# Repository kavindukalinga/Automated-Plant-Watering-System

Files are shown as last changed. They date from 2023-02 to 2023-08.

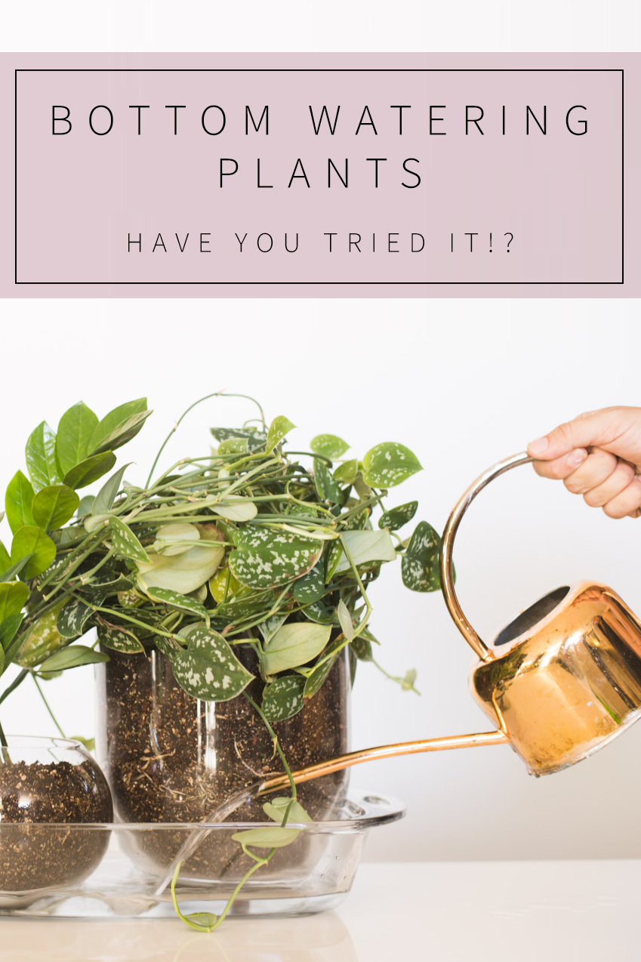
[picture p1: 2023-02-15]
Bottom-Watering-Plants.jpg

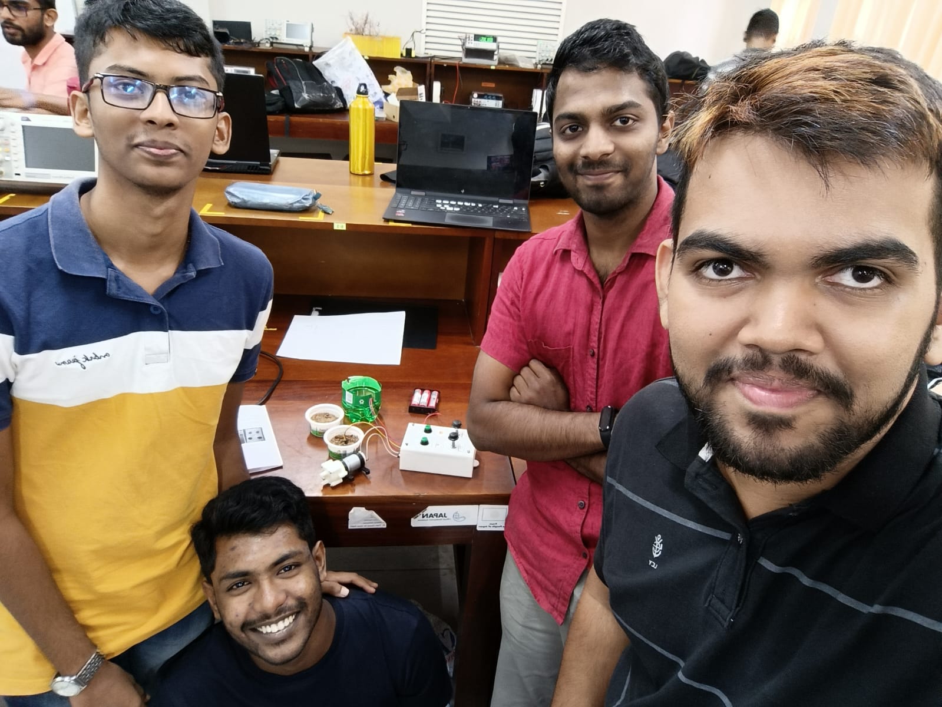
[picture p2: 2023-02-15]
Team - En04.jpg

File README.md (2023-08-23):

# Automated Plant Watering System 
 This is the project we chose for the Engineering design project module in semester 2. (In20-S2-EN1190 - Engineering Design Project)
 
# our project 

## Abstract:
The Automated Plant Watering System is designed to be used in home gardening to water plants when the moisture level in the soil drops below a certain level. Our main objective for this project is to provide a perfect solution for the problem that we identified, and the product that we develop should be cost-effective, easily repairable, and durable. In order to realize the design, we used software such as CircuitLab, Altium, and SolidWorks. The circuit simulation is checked using the CircuitLab simulator. The PCB design is done using the Altium software, and the enclosure is designed using SolidWorks software.

## Introduction:
The Automated Plant Watering System is an innovative solution designed to provide efficient and reliable watering for plants. The system is a response to the economic crisis in Sri Lanka and the need to encourage people to cultivate their own food. Many people are unable to tend to their plants due to busy schedules, leading to plant death. The Automated Plant Watering System is an easy-to-use system that automates the process of watering plants, ensuring their growth and health.

## Functionality:
The Automated Plant Watering System is a complete analog electronic system that detects soil moisture and the amount of water in the tank. It is designed to operate based on soil moisture readings and water availability in the tank. The system has a sensor that detects the moisture in the soil and signals the motor to distribute water to the soil if it is dry. The motor is connected using a relay module, which controls the water flow to the plants. The system also has a water level sensor that detects the amount of water in the tank. If the water level in the tank is low, an alarm is triggered to alert the user. The alarm is manually turned off by the user when the water is refilled. The system also has a timer that the user can adjust to control the water flow to the plants.

## User Interface:
The Automated Plant Watering System has an easy-to-use user interface that consists of two buttons and two knobs. The first button turns on the system, and the second button turns on/off the alarm. The first knob is used to control the timer, and the second knob is used to adjust the soil sensitivity. The soil sensitivity knob adjusts the dryness of the soil that should be present before the system starts watering the plants. The system is user-friendly and requires minimal effort from the user.

## Conclusion:
In conclusion, the Automated Plant Watering System is an efficient and innovative solution to the economic crisis in Sri Lanka. It is an easy-to-use system that automates the process of watering plants and ensures their growth and health. The system is designed to operate based on soil moisture readings and water availability in the tank. The user interface is simple and requires minimal effort from the user. The Automated Plant Watering System is a cost-effective solution that promotes sustainable living and encourages people to cultivate their own food.  

### Visit My Blog [Here](https://kalingachandrasiri.blogspot.com/2023/02/automated-plant-watering-system.html)

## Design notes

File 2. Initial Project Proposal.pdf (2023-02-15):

# Automated Plant Watering System

## PRODUCT PROPOSAL

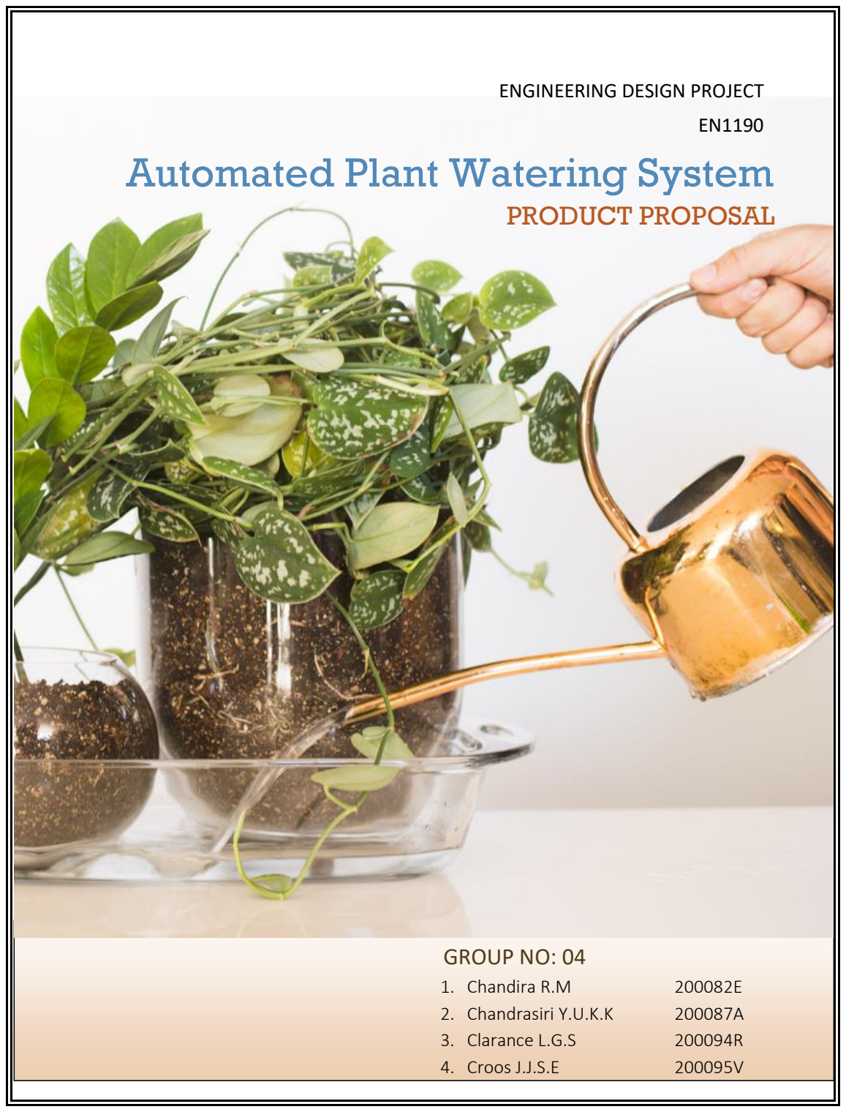
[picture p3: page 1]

ENGINEERING DESIGN PROJECT EN1190

## GROUP NO: 04

1. Chandira R.M | 200082E
2. Chandrasiri Y.U.K.K | 200087A
3. Clarance L.G.S | 200094R
4. Croos J.J.S.E | 200095V

## PROBLEM

Due to the prevailing economic instability in our country, there is an urgent need to increase the national production rate. To suppress the food crisis government has advised public to engage in home gardening. But it appears to many as a impossible task to manage this among their busy schedules.

## SOLUTION

Proposed solutions,

1. Greenhouse control system
2. User notifier on taking care of plants
3. Automated plant watering system

We finally agreed on developing an automated plant watering system.

## GOAL

Our main goal is to encourage people for more home gardening at least to meet their daily needs in the time of this crisis and beyond. We wish to develop this product affordable as much as possible while people in our country going through an economic crisis. This product will be user friendly, easy to repair and easy to reproduce with less resources.

## TARGET USERS

Government and Private sector workers, especially low-income people

## DESIGN SPECIFICATION

Our sensors are measuring the moisture level of soil and when the soil get dried than the threshold level, it triggers the irrigation system to water the plant.
And this automated system notifies the user to refill the water reservoir when the water level is low. And our whole electronic and electrical components of our system is protected by enclosure which is watertight and have resistance to all damaging factors of both indoor and outdoor environment. This system is friendly, in case of any repairing the user can easily access it.

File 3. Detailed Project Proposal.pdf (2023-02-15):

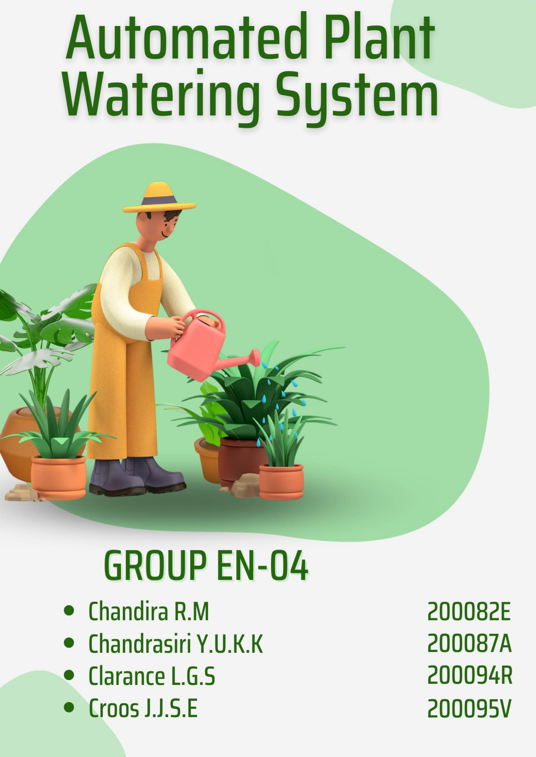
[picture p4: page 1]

# Content

## 1.Introduction

## 2.Proposed Solutions

## 3.Idea Validation

## 4. Survey Results

## 5.Technical Specifications

## 6.Technical Feasibility

## 7.Product Architecture

## 8. Enclosure Design

## 9.Marketing and Sales and Beyond

## 10.Project Budget

## Introduction

Due to the prevailing economic crisis in our country, we are facing unprecedented food shortages, so there is an urgent need to increase the national production rate to overcome food scarcity and malnutrition among children. To suppress this food crisis, the government has advised the public to engage in home gardening. “Amid the fuel crisis and looming food crisis, the government has decided to declare Friday as a holiday for State employees except for those who are engaged in providing essential services and to allow them to engage in agricultural activities in their home gardens." - [published on DailyMirror 15th June 2022]. By doing home gardening, people will get their daily essential nutrition at a minimum cost. But it appears to many (government and private sector workers) as an unthinkable task to manage this among their busy schedules because home gardening is something that needs continuous monitoring and extensive care.

So, as undergraduates of the Electronic and Telecommunication Department, University of Moratuwa, we are planning to design an electronic device which can be used as a solution to this problem, and we are very much concerned about the cost because the device that we are constructing should be affordable for everyone, including low-income receivers.

## Proposed Solutions

After brainstorming, we have arrived at some feasible options that can be done within an 8 - 10 weeks period.

### 1. Greenhouse control system:

An automated system targeting greenhouses to monitor and control humidity, temperature, and nutrition levels required for plants. This is done by using real-time sensors and IoT things that communicate wirelessly through Bluetooth or WiFi.

### 2. User notifier on taking care of plants:

An automated system to remind the user to water and add appropriate nutrition to plants. This can be accomplished by developing a device with a system that can send push notifications to the user's mobile.

### 3. Automated Plant Watering System:

Automatic plant watering systems that can water plants when the moisture level in the soil drops below a certain level (which can be adjusted by the user) and notify the user to refill the watering container.

## Idea Validation

When we enquired about the problem, we got some solutions. But every solution will not be executed perfectly. There are many reasons for each solution to be avoided.

When considering the greenhouse as a solution, according to the current price rate (24.06.2022), the cheapest functional greenhouse requires around 35000 LKR to assemble. In the case of repairing, the cost of the repair is also high, like its price. which is a three-quarter of many government staff's salaries. Because of the initial investment, it is not suitable for low-income families.

We need a backyard to set up a greenhouse. But most middle-class families don't have a backyard because most of them are in apartments, and others have limited space.

And there are some products, like

1. Garden cloche, 6 pack plant protect bell cover mini greenhouse (Rs 8,266)
2. Portable garden greenhouse outdoor warm greenhouse (Rs.19,260)

and more. Nothing is easily affordable for low-income families.

The second solution, developing a system to notify the user about watering plants and adding enough nutrition on time, had to be disregarded because of the availability of such apps in the marketplace. There are many apps available, but only a very few can be used without any hassle. Here the problem is, even if we are reminded to water the plant, when we out of home, it is not useful all the time, So we had to avoid these options.
Among all the solutions we had, we came up with designing the “Automated plant watering system” after we researched all our solutions very thoroughly. We considered mainly the cost per product, durability, repairability, and customizability. While we are comparing our product with other solutions and the products currently available in the market, the price of our product is the key factor to attract buyers so we figured out that we would be able to design our product very much affordable when we compared it with the cost of other similar products in the market. And when people buy a product, they should be able to repair it quickly if there are some minor issues. In our case, the product can be easily repaired and has less complexity than other products. For example, if there are issues with greenhouses, it is very hard to get them back to their original condition and it will cost a high amount as well. With this Automated plant watering system, we can water and maintain home gardens in 1m2 area, so it can be manageable in apartments. And it will be easy to reproduce with fewer resources.
Unlike other similar products which are already on the market, components and parts of our product are available in the local market. Therefore, users can replace parts very easily. This product is designed to be splash and dust-proof. The enclosure will protect circuits and electronic components from dry and wet environments.
And our product is easily customizable as well. Users can customize the water level, notifications, and some other stuff as they want, unlike other fixed products and application software.

Even though it is a low-cost product, it can be upgradable according to budget and user expectations. We are planning to add a timer as a refinement to our product, so it will allow our product to work only for a limited time each day, so it can save water and other resources. And we are discussing adding a feature to adjust the volume of water released by the system according to the specific plants. Plants should not be watered too much or too little. In hot weather, it may be tempting to repeatedly water plants, which can adversely affect plant growth. Hence, controlling watering frequency and amount appropriately with a product like ours is a must.
In conclusion, after thorough research using several media, the initial project idea was refined and redefined to better suit the current requirements of the intended users.

## Survey Results

After we built up our idea, we wanted to know about the real situation among our targeted people. So, we conducted a survey through Google Form. The survey is enough to justify our proposed problem and our finalized solution. So we came out of our assumption and strongly moved through it with the evidence of the survey. We finalized our decision with the responses of 170 targeted users.

From the conducted survey, more than three fourth of the population currently engages in home gardening.

Most of the respondents were informed that sometimes they have time to take care of their plants, which is not ideal for cultivation. Many plants, at their young age, are highly sensitive to the rate of watering. Without taking care of such plants daily, they can yield poor crops. Hence, it is clear from our responses that people are not inclined to invest in taking care of their plants consistently, and the need for a product like an automatic plant watering system is very high.

Figure 1: Responses on engaging in home gardening

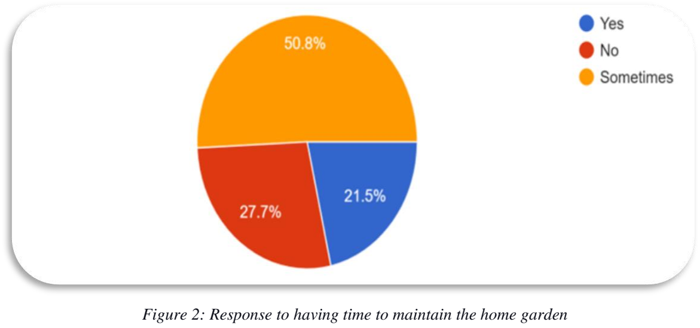
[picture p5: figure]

Even though similar products are widely present in the market, a significant number of responses indicate a preference for a low-cost automatic plant watering system.

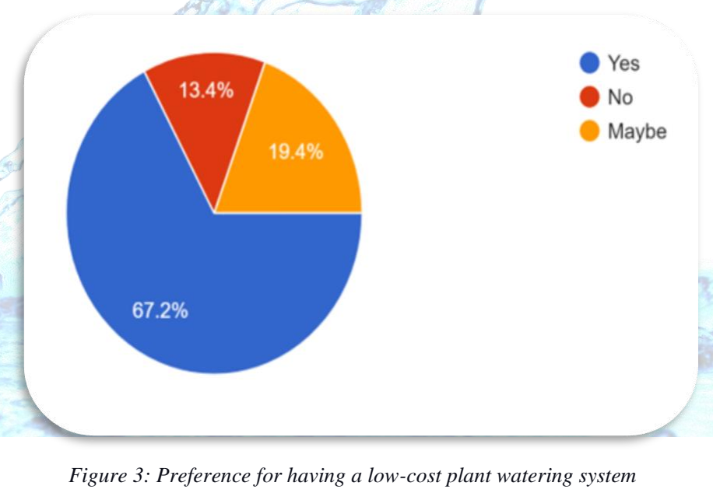
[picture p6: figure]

Our initial plan was to build a system where users needed to check the water level of the container and refill as required to reduce the cost. But the survey showed users prefer to be notified when the water level is empty as it reduces user intervention in plant maintenance.

Figure 2: Response to having time to maintain the home garden

Figure 3: Preference for having a low-cost plant watering system

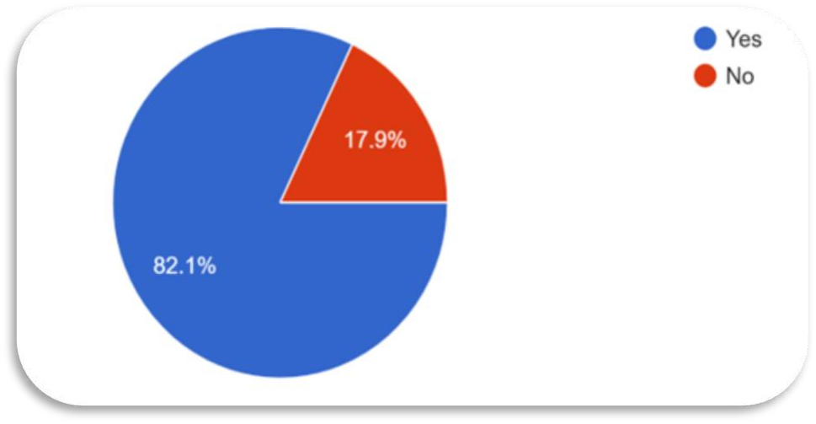
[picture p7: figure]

## Technical Specifications

Performance in quantitative terms.

NE555 timer initial error of timing -3%

Power consumption

LM324 – +/- 60mA, 9V

NE555 – 250mA, 9V

Motor – 12V, 8W

Product dimensions 120mm * 80mm *25mm

Weight - 250g

Lifetime of the product: 6 months for circuit

Warranty terms:

1. The product is only splash resistant to water and does not expose the system to water for extended periods of time.
2. Any physical damage done by the user will not be covered under the warranty.
3. Water pumps that receive no warranty should immerse the pump in a water reservoir while in use.

Figure 4: Preference for the ability of the system to notify when the

## Technical feasibility

Performance requirements

The system is an analogue system; hence it needs no software implementation.

The timer circuit can provide a pulse for up to 11 ms.

The sensitivity of the probes (soil) can be adjusted and probes for water sensitivity is calibrated while preparing the circuit but can be tuned by the user if required.

The motor is capable of pumping water up to 5 m vertically at a flow rate of 600L/H.

The system can provide up to 1.5 liters of water per single operation.

## Product Architecture

### Block diagram

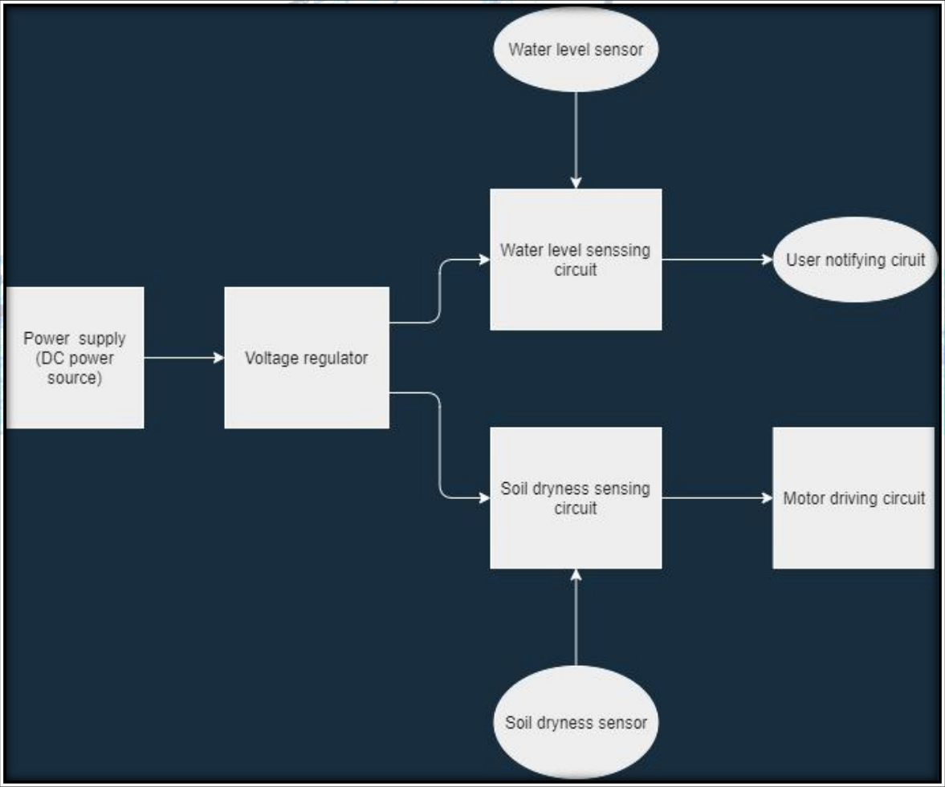
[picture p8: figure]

Figure 5: Block diagram representation

### Circuit Diagram

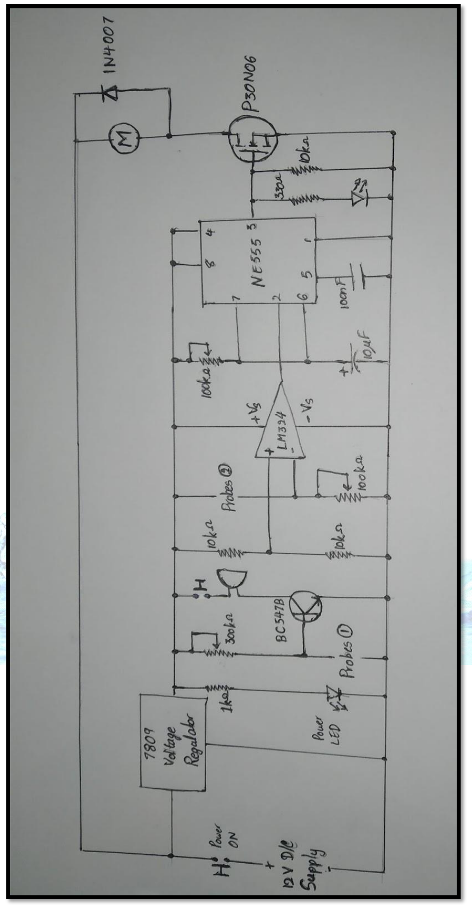
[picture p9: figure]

Figure 6: Circuit

## Enclosure Design

The enclosure contains two knobs (to control soil dry sensitivity and watering duration), two holes for 2 LEDs (indicates Power ON and motor ON), two push switches (Power On/Off and water sound On/Off), a wire connector (6 wires), and a wire connector for power supply. Inside, it contains 4 plugs, which we can use to connect the lid to the cover.
The size of the enclosure only depends on the size of the PCB and other circuit components, so there will not be a massive enclosure. It is a very lightweight one with an easy-to-handle size.
- Color: Mostly Gray and Black
- Material: Plastic

### UI and UX

There is a push switch (Power On/OFF) to Power On the product. When the product is powered on, the LED (Power On) will be on.
There are 2 knobs to control soil dry sensitivity and watering duration. The user needs to adjust the soil dry sensitivity according to the nature of the soil and the watering duration according to the nature of the plant.
The other LED is for indicating that the motor is whether On or Off. The LED is On while the motor is On. Otherwise, it is Off.
The other push switch is for controlling the buzzer. The buzzer is activated when the water level is low. If the user wants to deactivate the buzzer, they can do so using the push button. We label every UI control so that users will not get confused while using it, and it has a very easy-to-use UI.

### Initial Sketches

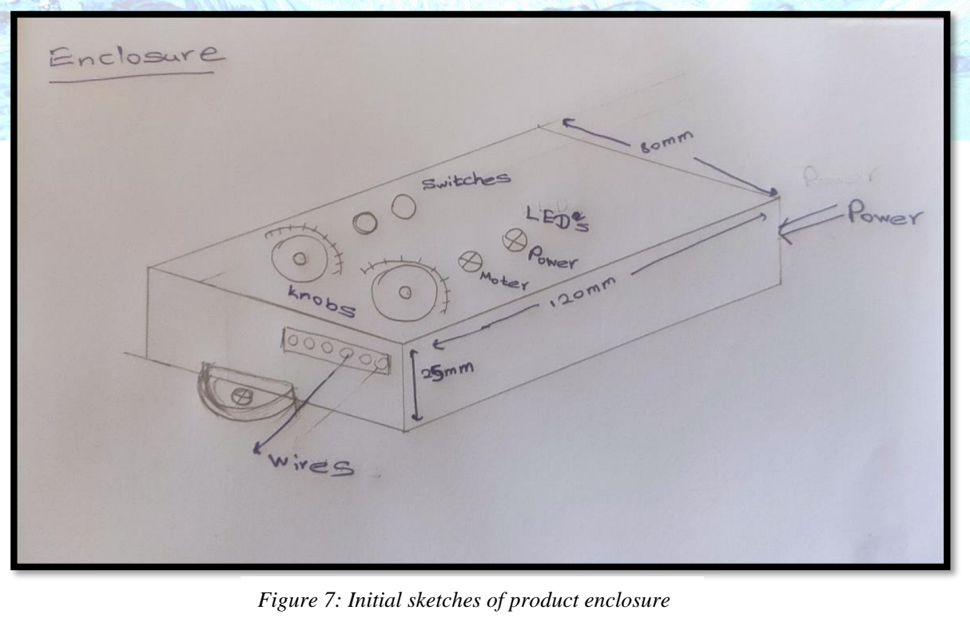
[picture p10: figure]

Figure 7: Initial sketches of product enclosure

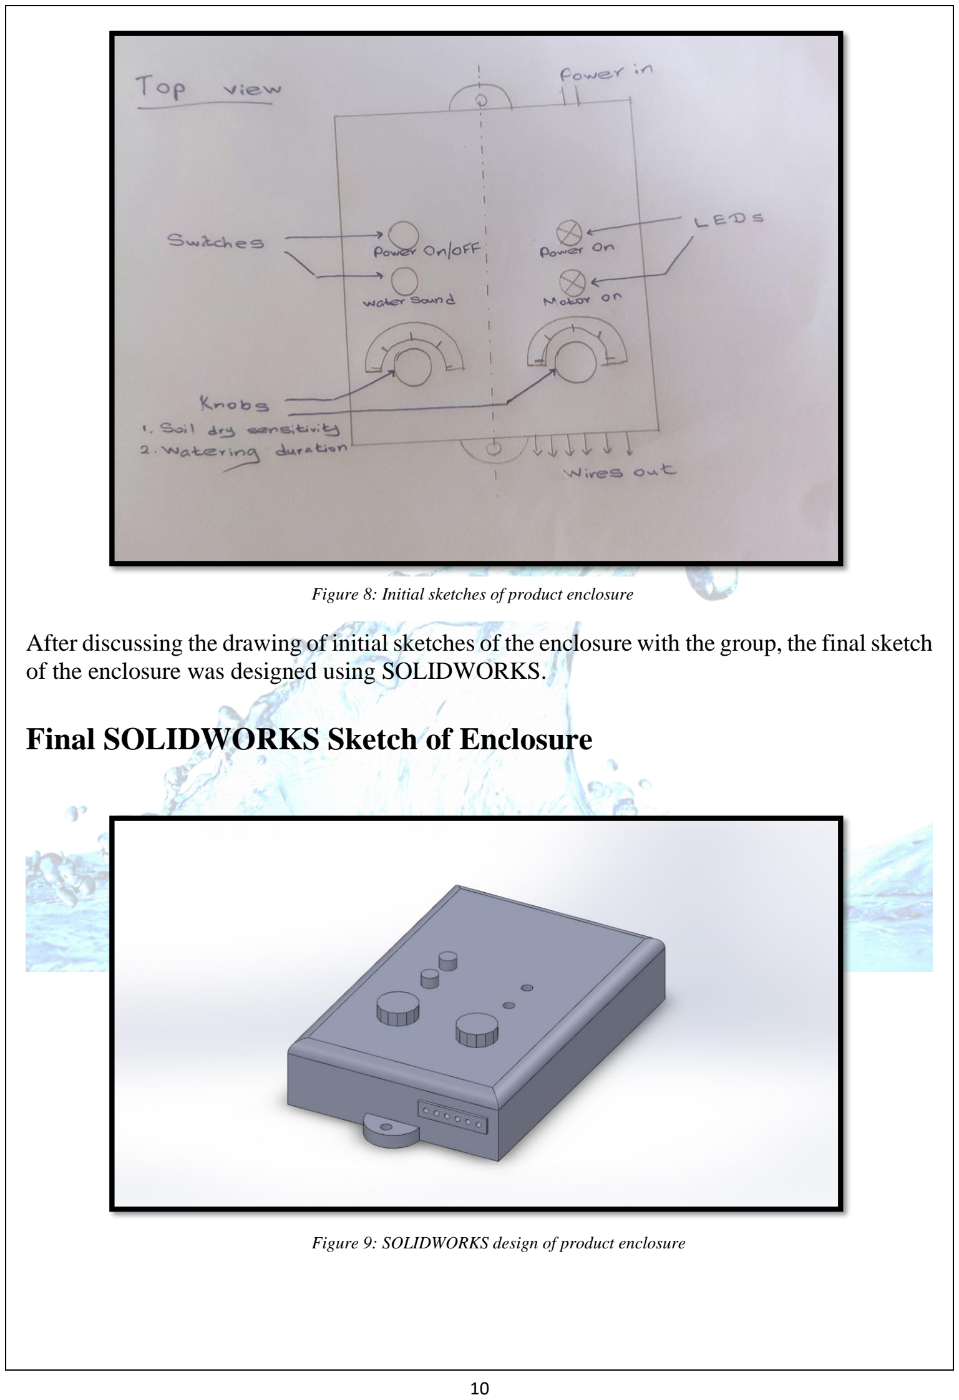
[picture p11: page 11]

After discussing the drawing of initial sketches of the enclosure with the group, the final sketch of the enclosure was designed using SOLIDWORKS.

### Final SOLIDWORKS Sketch of Enclosure

Figure 8: Initial sketches of product enclosure

Figure 9: SOLIDWORKS design of product enclosure

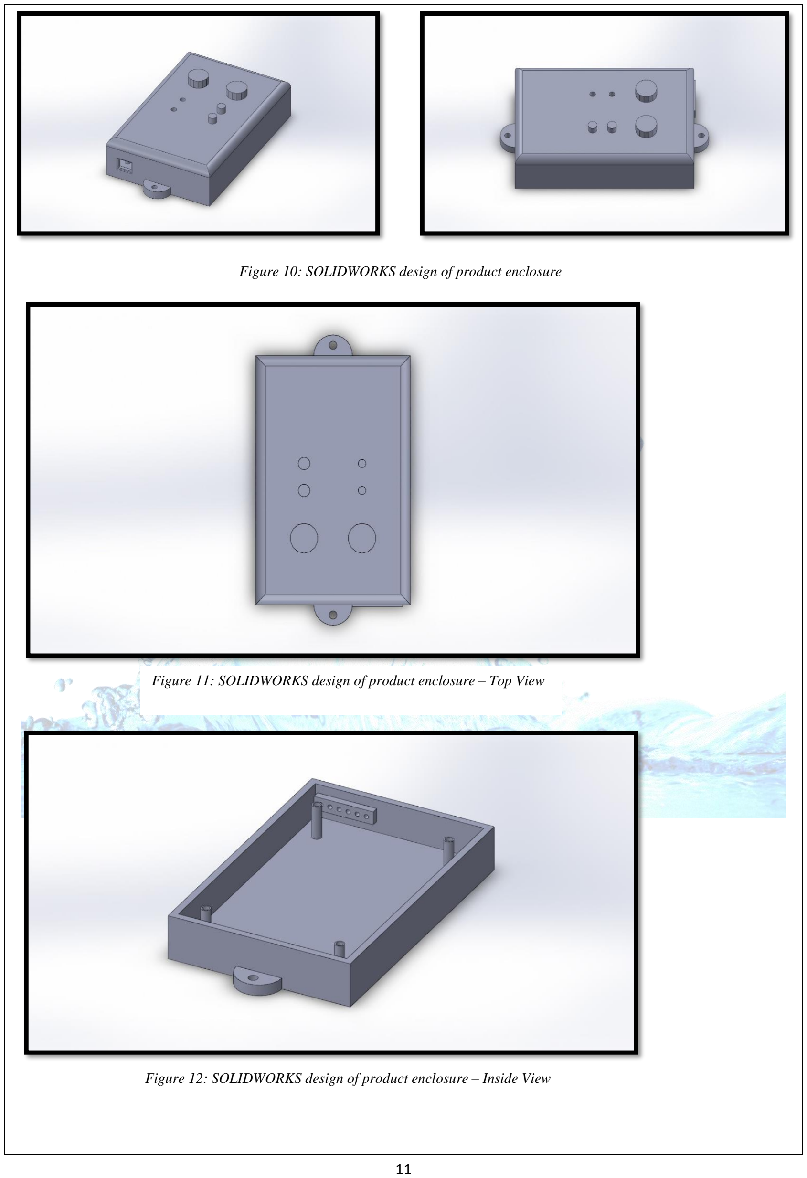
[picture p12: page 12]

Figure 10: SOLIDWORKS design of product enclosure

Figure 11: SOLIDWORKS design of product enclosure – Top View

Figure 12: SOLIDWORKS design of product enclosure – Inside View

## Marketing and Sales and Beyond

### Product packaging

We are going to provide our product as pre-assembled. So, the user will receive it as a completed one. So, we planned as below.
- Initially the user doesn't need to open the enclosure so that it will be closed.
- The enclosure will be covered by polythene to protect the electronic circuits from the wet environment before it has been assembled.
- The probes are provided inside the box but separately from the enclosure, it won't be covered with polythene, but the ports of the probes will be covered.
- Then whole components will be packed within a cardboard box.
- The user manual will be printed in the cardboard box.

### Maintenance

After the user sets up the system, it doesn't need daily maintenance. But the user is required to check the sensitivity and timer once a monthto protect the plants.
The user should be aware of other impacting factors on plant growth.
Our system is maintaining only the humility of sand.

### Repair

There is a power LED and a motor LED on the enclosure to indicate the power status and functional status of the motor to the user.
If one of them does not work, then the user will need the help of a technician to troubleshoot it.

### Reuse/Recycle

Since we are using a plastic enclosure, the probability of damaging the enclosure is very low. So, even if the components have any failures, we can replace them with new ones or repair them and reuse the system.
We are only using plastic, electronic components, and cardboard in our product. So plastic and cardboard can be recycled. All the electronic components can be recycled unless they are refurbished /reconditioned (repaired, upgraded) and used again.
We are using recyclable plastics for the enclosure, so we can recycle the enclosure and PCB. The PCB recycling machine is specially designed for recycling circuit boards to get the metal.

### Disposal

All the electronic components can be disposed of as e-waste as there are many ways to dispose of e-waste nowadays

## Project Budget

Components | Cost per Component | Cost
DC jack - 1 | Rs 90.00 | Rs 90.00
7809 Voltage regulator - 1 | Rs 60.00 | Rs 60.00
300kΩ pots - 1 | Rs 250.00 | Rs 250.00
BC547B transistor - 1 | Rs 10.00 | Rs 10.00
9V buzzer - 1 | Rs 60.00 | Rs 60.00
330Ω resistor - 1 | Rs 1.00 | Rs 1.00
10kΩ resistors - 3 | Rs 1.00 | Rs 3.00
100kΩ B potentiometers - 2 | Rs 40.00 | Rs 80.00
100uF capacitor - 1 | Rs 10.00 | Rs 10.00
100nF capacitor – 1 | Rs 4.00 | Rs 4.00
LED yellow/red – 2 | Rs 6.00 | Rs 12.00
Push switch – 1 | Rs 50.00 | Rs 50.00
1N4007 diode – 1 | Rs 3.00 | Rs 3.00
NE555 timer – 1 | Rs 30.00 | Rs 30.00
LM324 IC – 1 | Rs 40.00 | Rs 40.00
P30N06 N channel MOSFET – 1 | Rs 90.00 | Rs 90.00
Total | | Rs 793.00

Table 1: Cost for components

PCB printing cost:

As per the current market for PCB printing, Rs. 6.00 is charged per single point. So it will cost us around Rs. 500.00

Enclosure Cost:

It costs Rs. 500.00 for 3D printing for only one product. But for mass production, we don’t want to go for 3D printing. So, the enclosure cost can be minimized.

### Product Price

As we are very much concerned about the price of the product, we are thinking of a product price of around Rs 1800.00

### Marketing

The targeted users are
-Government and Private sector workers - especially low-income people -Who is fond of using technology in their day-to-day life.

Strategy
-Advertising through social media.
-Creating a website and promoting the product through the website. -Use influencers

Selling method
-Sold in local markets like hardware shops and electronic shops.
-Sold through the website and other online shopping pages (Daraz, Amazon)

### Sales Price

We have assumed our selling price as Rs. 2100.00, which includes the following
- Manufacturing
- Components
- Packaging
- Marketing
- Profit

As of now we have decided our sales volume is 150. It may increase in the future with the feedback from our customers.
This is only a proposal. We can minimize the production cost based on the targeted user’s feedback and the related future work.

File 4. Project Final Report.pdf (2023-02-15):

## Department of Electronic and Telecommunication Engineering University of Moratuwa

EN1190: Engineering Design Project

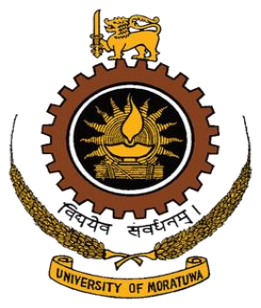
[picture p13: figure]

# PROJECT REPORT AUTOMATED PLANT WATERING SYSTEM

## Group EN-04

1. Chandira R.M. 200082E
2. Chandrasiri Y.U.K.K. 200087A
3. Clarance L.G.S. 200094R
4. Croos J.J.S.E 200095V

## October 7, 2022

## Abstract

The Automated Plant Watering System is designed to be used in home gardening to water plants when the moisture level in the soil drops below a certain level. Our main objective for this project is to provide a perfect solution for the problem that we identified, and the product that we develop should be cost-effective, easily repairable, and durable. In order to realize the design, we used software such as CircuitLab, Altium, and SolidWorks. The circuit simulation is checked using the CircuitLab simulator. The PCB design is done using the Altium software, and the enclosure is designed using SolidWorks software.

## Table Of Contents

## 1. Introduction

Due to the prevailing economic crisis in our country, we are facing unprecedented food shortages, so there is an urgent need to increase the national production rate to overcome food scarcity and malnutrition among children. To suppress this food crisis, the government has advised the public to engage in home gardening. “Amid the fuel crisis and looming food crisis, the government has decided to declare Friday as a holiday for State employees except for those who are engaged in providing essential services and to allow them to engage in agricultural activities in their home gardens." - [published on DailyMirror 15th June 2022]. By doing home gardening, people will get their daily essential nutrition at a minimum cost. But it appears to many (government and private sector workers) as an unthinkable task to manage this among their busy schedules because home gardening is something that needs continuous monitoring and extensive care.

So, as undergraduates of the Electronic and Telecommunication Department, University of Moratuwa, our main aim was to create a product that can be used as a solution to this problem. At the same time, we were very much concerned about the cost, because the device that we are constructing should be affordable for everyone, including low-income receivers.
Our product can water plants when the moisture level in the soil drops below a certain level (which can be adjusted by the user) and notify the user to refill the watering container.

Figure 1.1 depicts a block diagram of the device

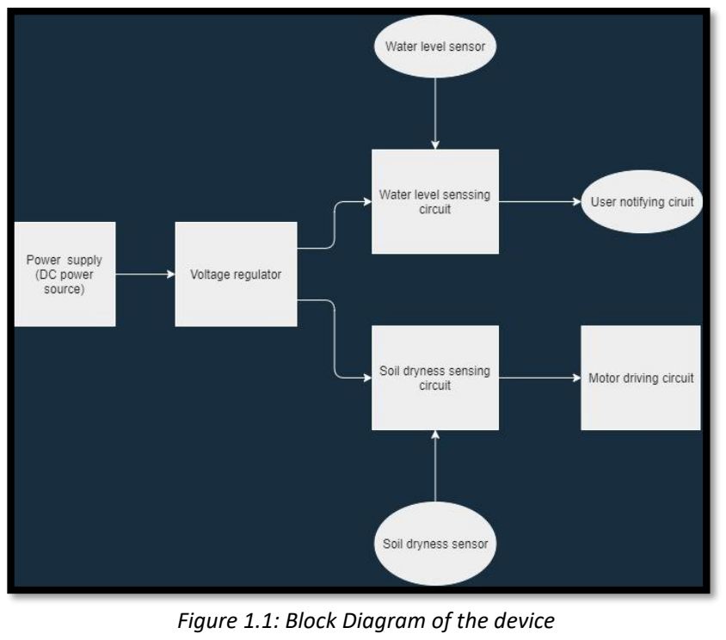
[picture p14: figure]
Figure 1.1: Block Diagram of the device

## 2. Method

## 2.1. Overview

The development of this project was done in four stages. They are,

1. Simulation
2. Breadboard Implementation
3. Designing and Fabricating the PCB
4. Enclosure Design

## 2.1.1. Simulation

Initially, the circuit was made in the CircuitLab simulator, an online tool. It was tested by checking the voltage across the circuit elements and current through the components, and we ensured that the circuit was working properly.

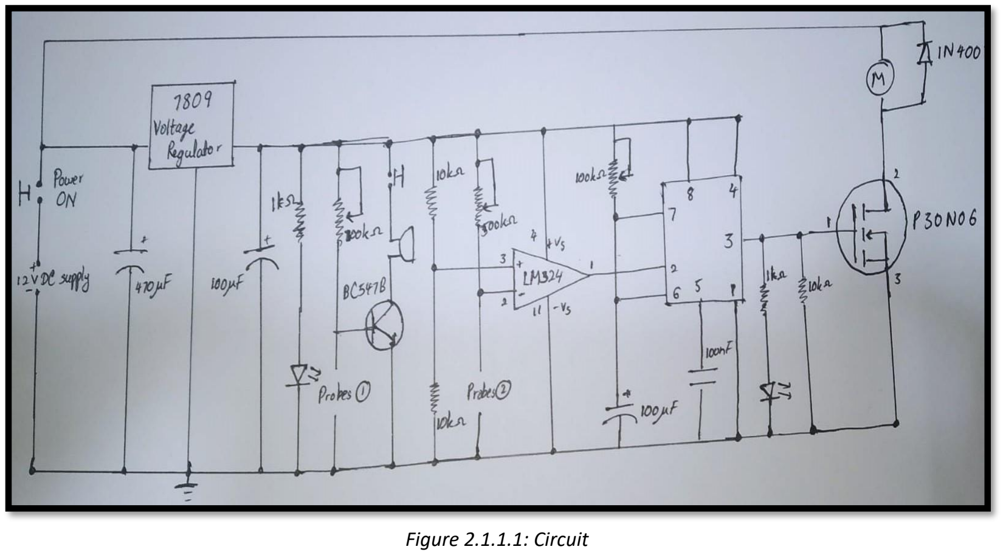
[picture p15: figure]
Figure 2.1.1.1: Circuit
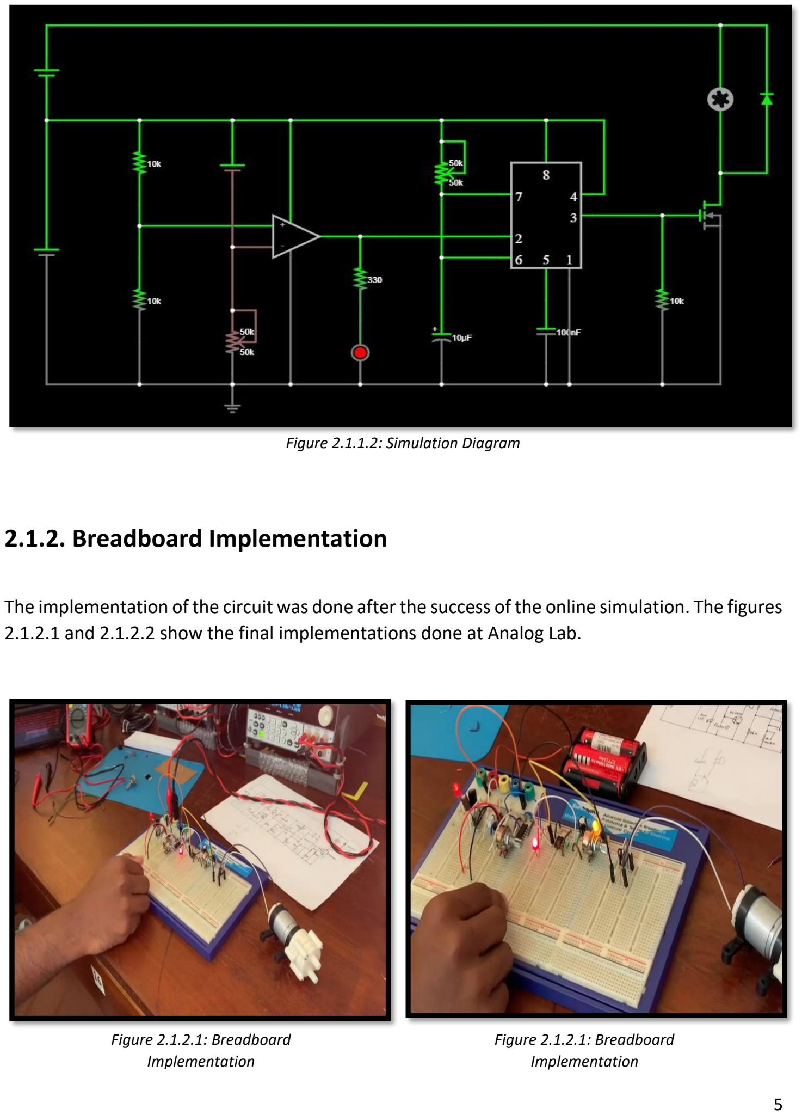
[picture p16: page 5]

## 2.1.2. Breadboard Implementation

The implementation of the circuit was done after the success of the online simulation. The figures 2.1.2.1 and 2.1.2.2 show the final implementations done at Analog Lab.

Figure 2.1.1.2: Simulation Diagram

Figure 2.1.2.1: Breadboard Implementation

Figure 2.1.2.1: Breadboard Implementation

## 2.1.3. Designing and Fabricating the PCB

PCB design was done using Altium software. In the schematic design, all the components and connections were made according to our CircuitLab simulation. A 2-layer PCB layout was designed to add more compactness to the design. A 1 mm route width and a 0.8 mm (minimum value) drill hole size were selected for the design. By using an online PCB trace width calculator (DigiKey), we justify the trace widths used for the PCB design. We printed the PCB from a PCB manufacturer. PCB soldering is done by us at Analog Lab.

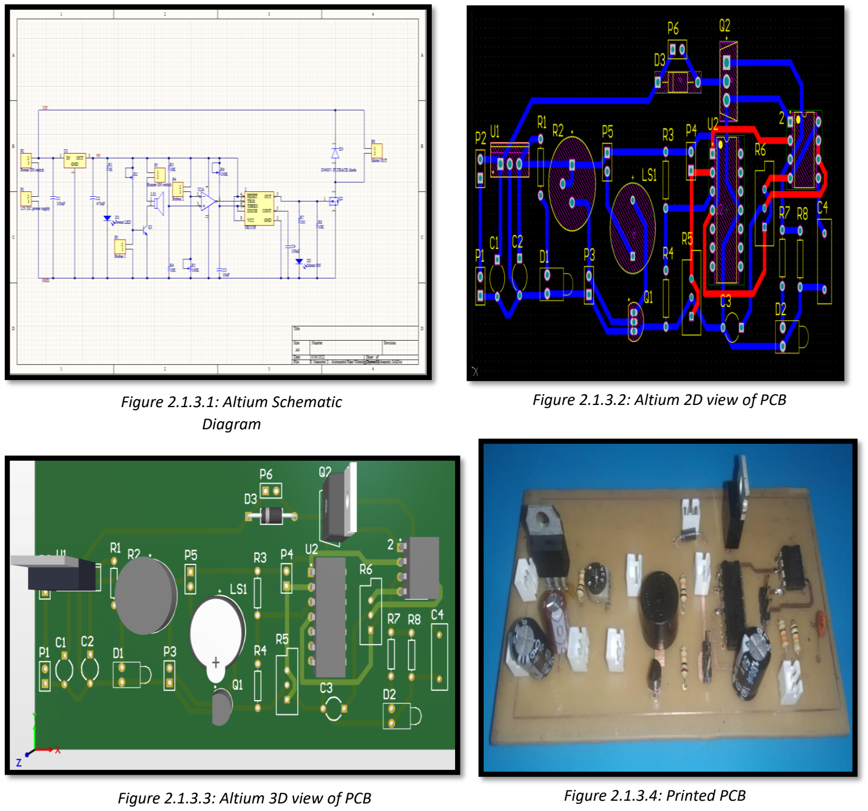
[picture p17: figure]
Figure 2.1.3.1: Altium Schematic Diagram; Figure 2.1.3.2: Altium 2D view of PCB

Figure 2.1.3.3: Altium 3D view of PCB | Figure 2.1.3.4: Printed PCB

## 2.1.4. Enclosure Design

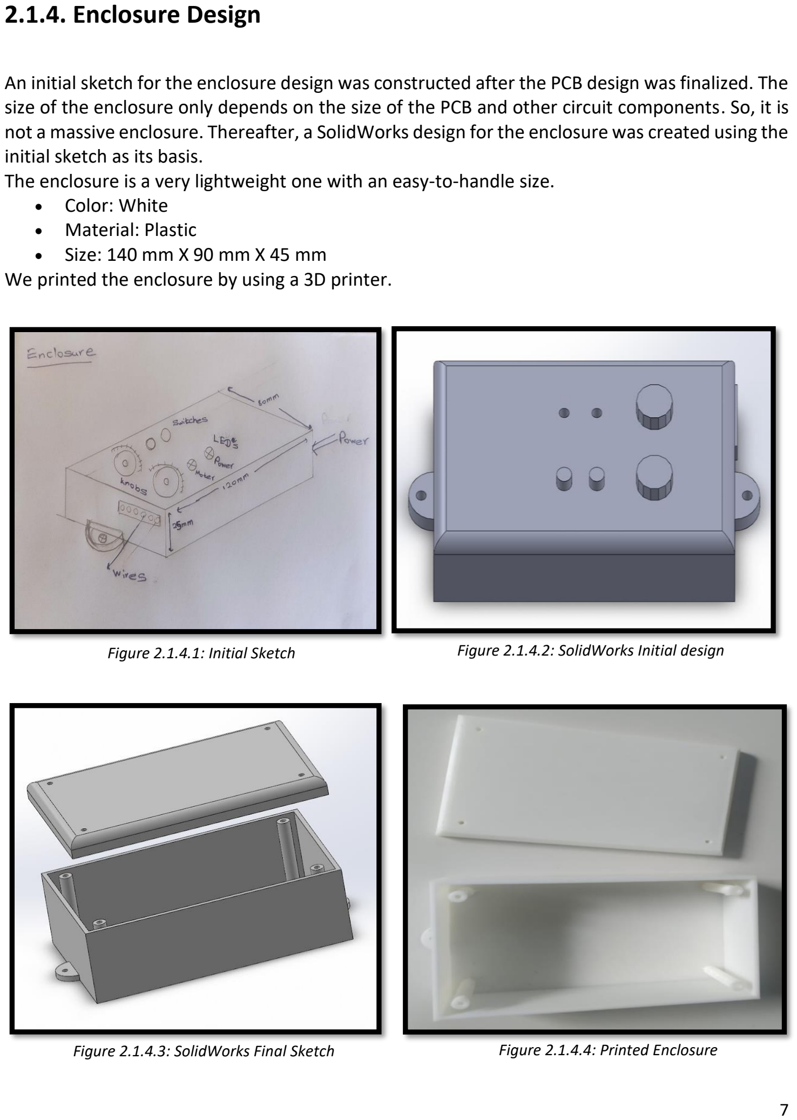
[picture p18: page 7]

An initial sketch for the enclosure design was constructed after the PCB design was finalized. The size of the enclosure only depends on the size of the PCB and other circuit components. So, it is not a massive enclosure. Thereafter, a SolidWorks design for the enclosure was created using the initial sketch as its basis.
The enclosure is a very lightweight one with an easy-to-handle size.
- Color: White
- Material: Plastic
- Size: 140 mm X 90 mm X 45 mm
We printed the enclosure by using a 3D printer.

Figure 2.1.4.3: SolidWorks Final Sketch

Figure 2.1.4.2: SolidWorks Initial design

Figure 2.1.4.4: Printed Enclosure

Figure 2.1.4.1: Initial Sketch

## 2.2. List of Components

Components | Quantity
7809 Voltage regulator | 1
300kΩ pots | 1
BC547B transistor | 1
9V buzzer | 1
330Ω resistor | 1
10kΩ resistors | 3
100kΩ B potentiometers | 2
100uF capacitors | 2
470uF capacitor | 1
100nF capacitor | 1
LED yellow/red | 2
1N4007 diode | 1
NE555 timer | 1
LM324 IC | 1
P30N06 N channel MOSFET | 1

## 2.3. Project Expenditure Account

Expenditures | Amount
Components | Rs. 1160
PCB print | Rs. 550
Enclosure 3D print | Rs. 2000
Total | Rs. 3710

## 2.4. User Interface

There is a push switch (Power On/OFF) to Power On the product. When the product is powered on, the LED (Power On) will be on. There are 2 knobs to control soil dry sensitivity and watering duration. The user needs to adjust the soil dry sensitivity according to the nature of the soil and the watering duration according to the nature of the plant. The other LED is for indicating that the motor is whether On or Off. The LED is On while the motor is On. Otherwise, it is Off. The other push switch is for controlling the buzzer. The buzzer is activated when the water level is low. If the user wants to deactivate the buzzer, they can do so using the push button. We label every UI control so that users will not get confused while using it, and it has a very easy-to-use UI.

## 2.5. User Manual

- Maintenance
After the user sets up the system, it doesn't need daily maintenance. But the user is required to check the sensitivity and timer once a month to protect the plants. The user should be aware of other impacting factors on plant growth. Our system is maintaining only the moisture level of the soil.
- Repair
There is a power LED and a motor LED on the enclosure to indicate the power status and functional status of the motor to the user. If one of them does not work, then the user will need the help of a technician to troubleshoot it.
- Reuse/Recycle
Since we are using a plastic enclosure, the probability of damaging the enclosure is very low. So, even if the components have any failures, we can replace them with new ones or repair them and reuse the system. We are only using plastic, electronic components, and cardboard in our product. So, plastic and cardboard can be recycled. All the electronic components can be recycled unless they are refurbished /reconditioned (repaired, upgraded) and used again. We are using recyclable plastics for the enclosure, so we can recycle the enclosure and PCB. The PCB recycling machine is specially designed for recycling circuit boards to get the metal.
- Disposal
All the electronic components can be disposed of as e-waste as there are many ways to dispose of e-waste nowadays.
- Warranty
6 months warranty for the components and 12 months warranty for the product functionality.

## 3. Results

The product functions as whole and gives expected results. It is tested in different environments under adequate conditions and observed its functionality. It is aligned to send out to the market.

## 4. Discussion

The system can be powered by different sources of power like a power pack or solar cell with 12V output.
The motor can be freely upgraded by the user to suit their use case, the system is even capable of supporting a 230V AC motor with an adequate relay.
The design can withstand rugged use cases and can withstand vibrations up to certain level without losing functionality.
The design is easy to open, and trouble shoot even by an amateur electronic enthusiast ensuring the longevity of the product.
The system compromises low cost easily found electronic components making it profitable to repair.
The system can support a variety of plants that grow in different regions of the country simply by changing the dials settings in the UI.
We are hoping to minimize the production cost based on the targeted user’s feedback and the related future work.

## 5. Bibliography

[Altium] (January 10, 2022). A Complete Design Walkthrough with Altium Designer. Retrieved from
https://www.altium.com/documentation/altium-designer/tutorial-complete-design-walkthrough
[Audas] (May 28, 2021). From Zero to PCB | using Altium Designer [Video File]. Retrieved from
https://youtu.be/6N2A6LtBWh0

[Electronics Tutorial]. 555 Timer Tutorial. Retrieved from https://www.electronics-tutorials.ws/waveforms/555_timer.html

[MySolidWorks] (June 6, 2022). Training Catalog. Retrieved from https://my.solidworks.com/training/catalog/list/2

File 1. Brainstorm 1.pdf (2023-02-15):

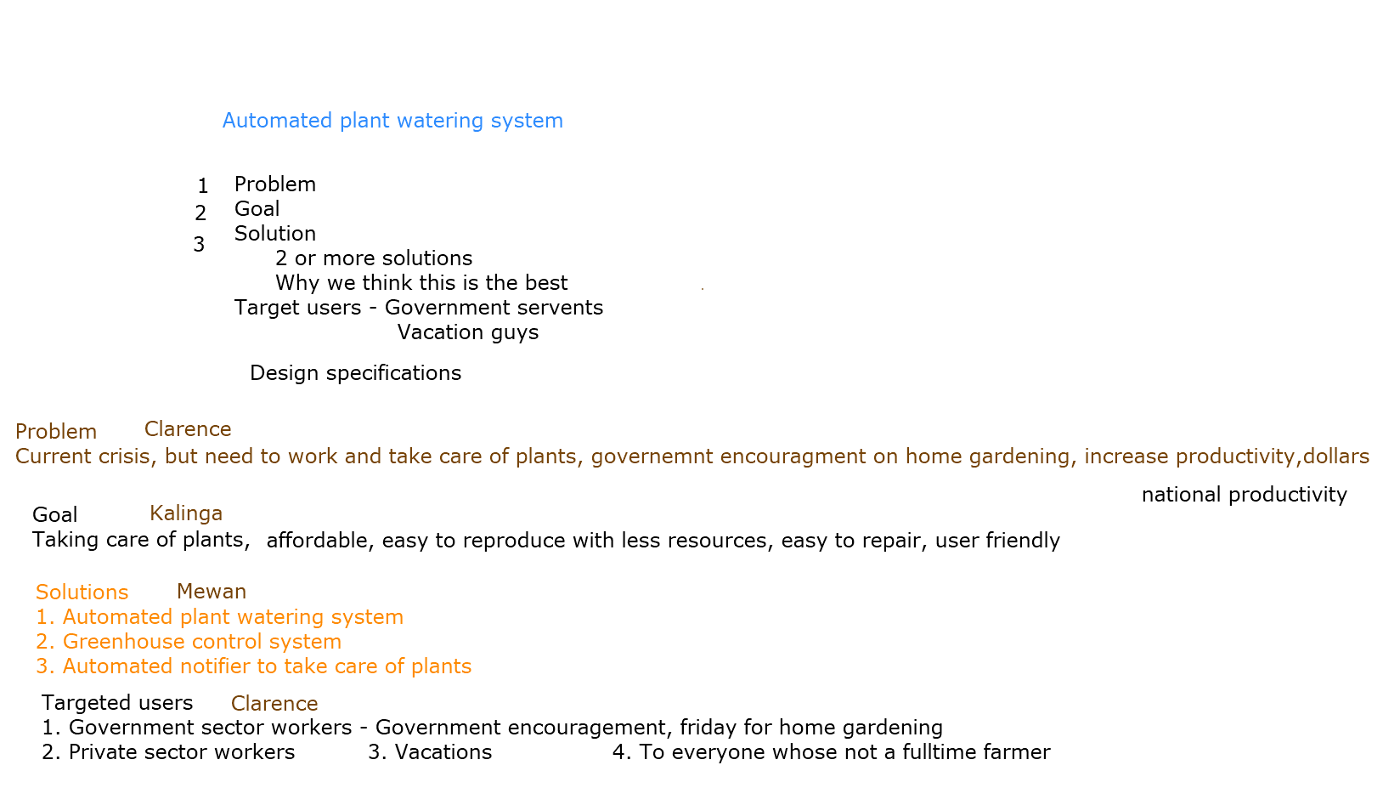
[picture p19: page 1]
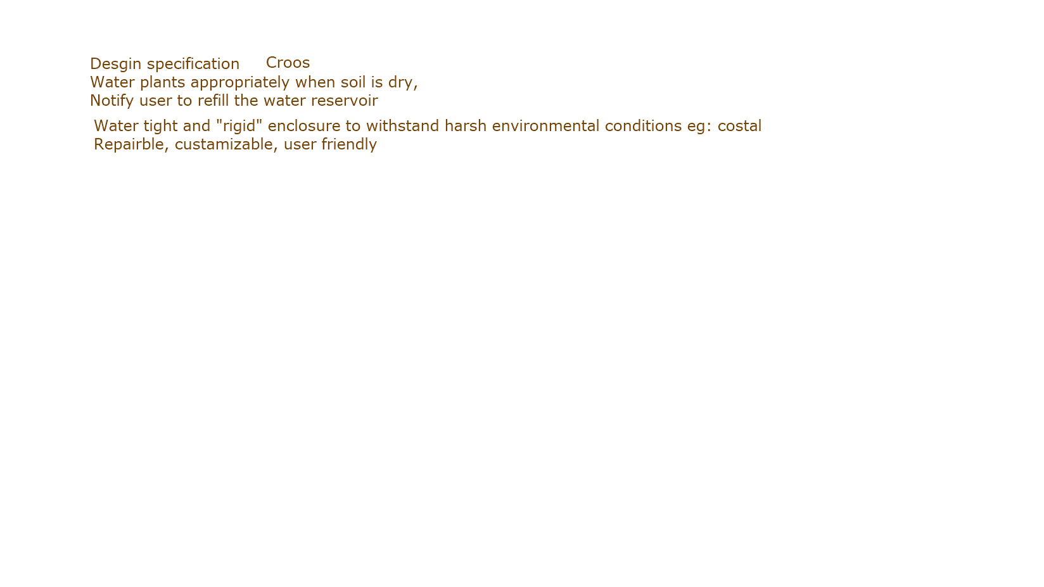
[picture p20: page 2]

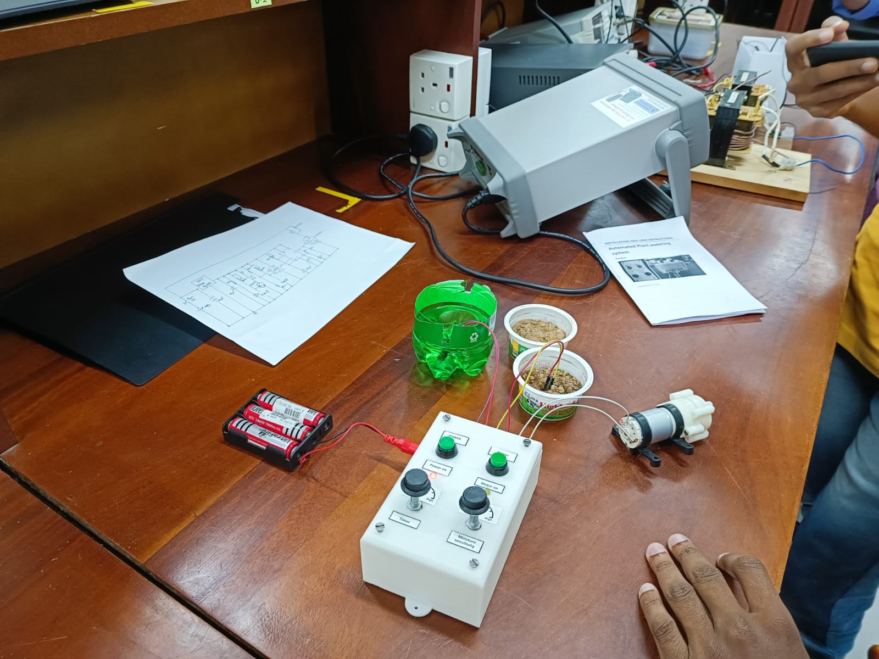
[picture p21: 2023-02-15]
5. Final Product.jpg

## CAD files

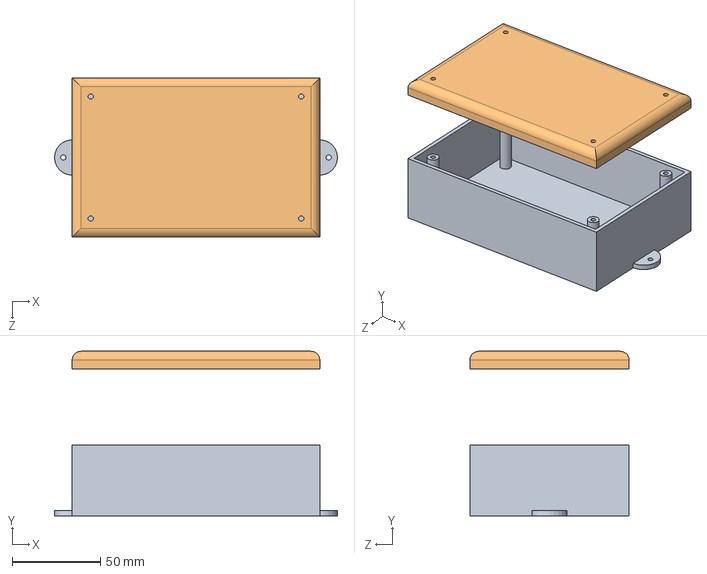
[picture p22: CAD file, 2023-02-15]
Project SOLIDWORKS Design Files/Final Design.SLDASM
160.0 x 93.0 x 90.0 mm
design pro2
design pro2 - Copy

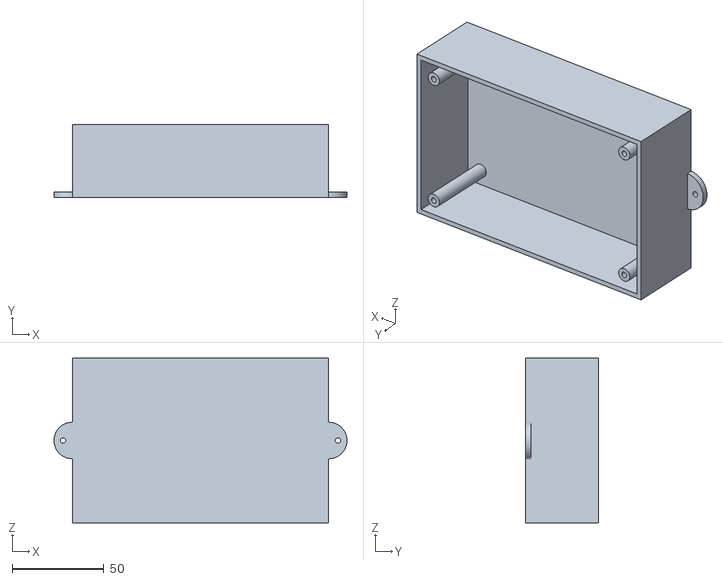
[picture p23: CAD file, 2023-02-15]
Project SOLIDWORKS Design Files/3D printing body.STL
159.9 x 40.0 x 90.0

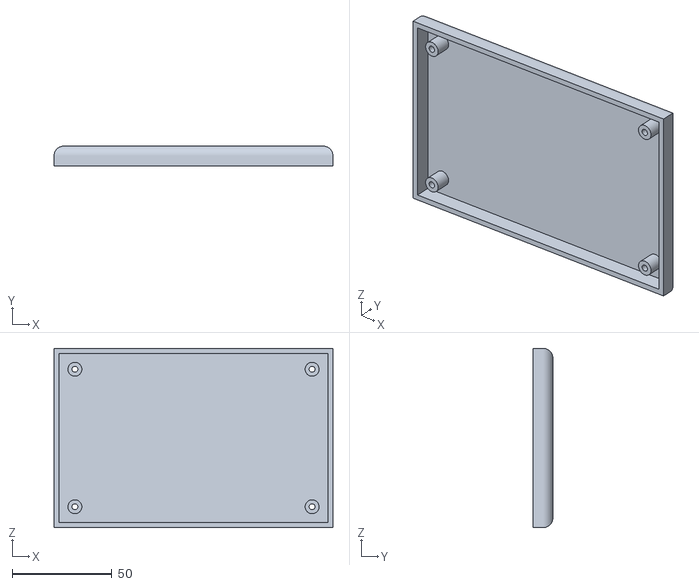
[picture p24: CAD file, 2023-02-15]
Project SOLIDWORKS Design Files/3D printing top.STL
140.0 x 10.0 x 90.0

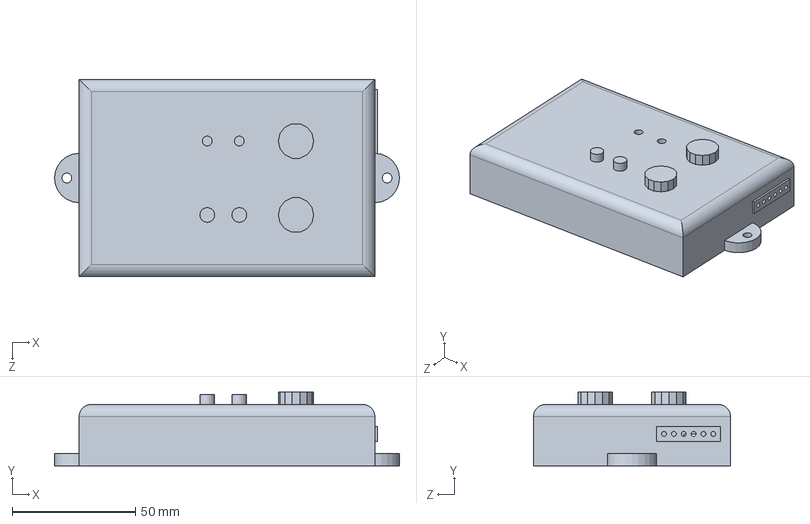
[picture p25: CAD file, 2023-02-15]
Project SOLIDWORKS Design Files/Project initial sketch.SLDPRT
140.0 x 30.0 x 80.0 mm

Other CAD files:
Project SOLIDWORKS Design Files/design pro2.SLDPRT
Project SOLIDWORKS Design Files/design pro2 - Copy.SLDPRT
